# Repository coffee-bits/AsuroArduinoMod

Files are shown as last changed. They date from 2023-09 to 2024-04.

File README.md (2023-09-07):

- [AsuroArduinoMod](#asuroarduinomod)
  - [Goal of the project](#goal-of-the-project)
  - [Problems so far](#problems-so-far)
    - [The old motors are dead](#the-old-motors-are-dead)
  - [State of the project](#state-of-the-project)
    - [Software](#software)
    - [Hardware](#hardware)

# AsuroArduinoMod
> This project is using an Arduino pro micro instead of the original Atmega8L

I own a very old robot education platform called [ASURO](https://de.wikipedia.org/wiki/ASURO)

The main problem using this good old little thing was the old Atmega8L microcontroller platfofm that is programed by avrgcc or Atmel Studio (tm) and loaded by a serial bootloader via an IR light communication channel.

I wanted to bring this in the next level of microcontroller platforms since the modern versions are much easier to use and program. Most of the new platforms unfortunately are using 3.3V but the Asuro has been designed for a logic level of 5V.

My choice was then a Arduino pro micro which uses 5V logic level, has an USB serial interface for communication and program download and its pinning and functionality is quite similar to the Atmega8L.

## Goal of the project
- Replace the old Atmega8L with a "modern" but similar platform: Arduino pro micro instead of the Atmega8L
- create a base system using all the hardware functionalities provided by the Asuro platform
- create a communication interface on the serial port with a simple API procotol to enable other controllers with, for example a WIFI interface or camera, to control the robot platform

## Problems so far
### The old motors are dead
I had to replace the old motors with newer ones. I found a nice and cheap all in one solution...that does not fit and needs a holding frame. So I constructed a frame prototype:

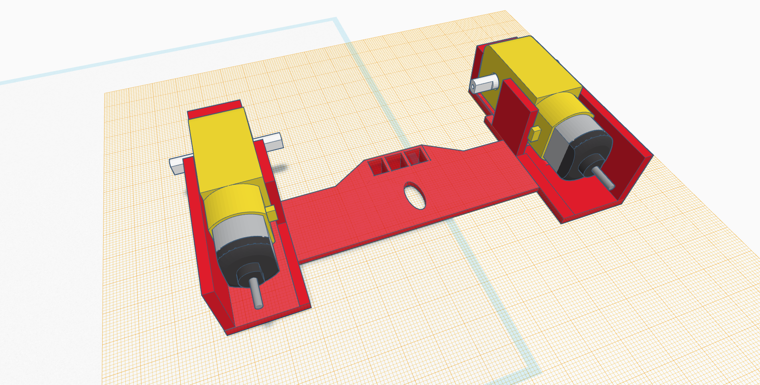
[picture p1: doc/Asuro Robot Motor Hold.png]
Asuro Robot Motor Hold


## State of the project
### Software
The software is currently in experimentl state. All Asuro interfaces are going to be testet with the new connections on the Arduino pro micro. The interface driver functions are going to be rewritten without the usage of the original api.

### Hardware
> connections
All hardware interfaces of the Asuro have been connected to according pins of the Arduino pro micro.

| Pin | Asuro | Arduino | Pin | Asuro | Arduino |
| --- | --- | --- | --- | --- | --- |
| 1 | Rset | \- | 15  | Motor 1 PWM | D6 |
| 2 | IR Receiver<br>SFH5110-36 | D2 | 16  | Motor 2 PWM | D5 |
| 3 | IR Diode -<br>SFH 415-U | GND | 17  | IR Diode +<br>SFH 415-U | D10 |
| 4 | Color LED | D7 | 18  | Motor 2_T7/8 | D13 |
| 5 | Taster Int | D3 | 19  | Motor 2 T5/6 | D9 |
| 6 | Motor 1_T1/2 | D11 | 20  | AVCC | n.a. |
| 7 | VCC | 5V | 21  | Aref | AREF |
| 8 | GND | GND | 22  | AGND | n.a. |
| 9 | Quarz | \- | 23  | Phototransistor T12 analog<br>LPT80A, Fototransistor, farbloses Gehäuse<br>LED D16 +<br>LED 5mm rot | A0 |
| 10  | Quarz | \- | 24  | Phototransistor T11<br>LPT80A, Fototransistor, farbloses Gehäuse<br>LED D15 +<br>LED 5mm rot | A1 |
| 11  | Motor 1_T3/4 | D12 | 25  | Phototransistor T10 analog<br>SFH 300 Fototransistor 5mm | A2 |
| 12  | LED Line | D4 | 26  | Phototransistor T11 analog<br>SFH300, Fototransistor 5mm | A3 |
| 13  | LED 13/14 +<br>IRL80A IR-LED rosafarbenes Gehäuse<br>LED 15/16 -<br>LED 5mm rot | D7 | 27  | Taster Analog Input | A4 |
| 14  | Color LED | D8 | 28  | Spannungsteiler 12k/10k | A5 |

> Prototype state

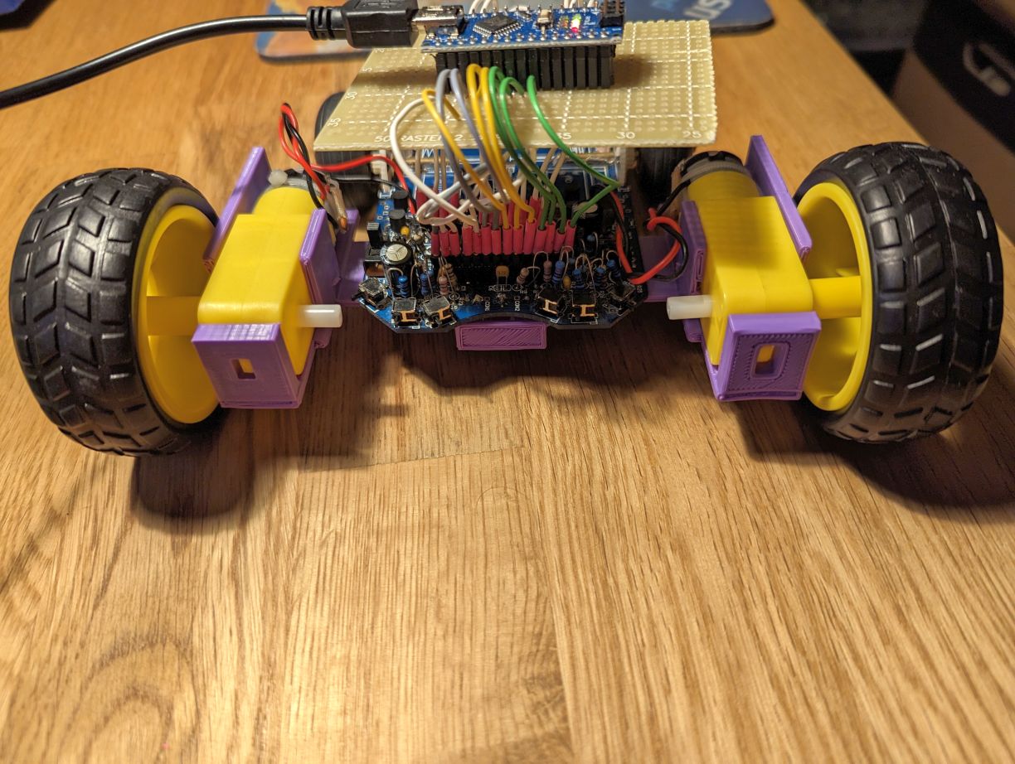
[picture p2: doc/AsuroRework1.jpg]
Asuro Prototype 1.1

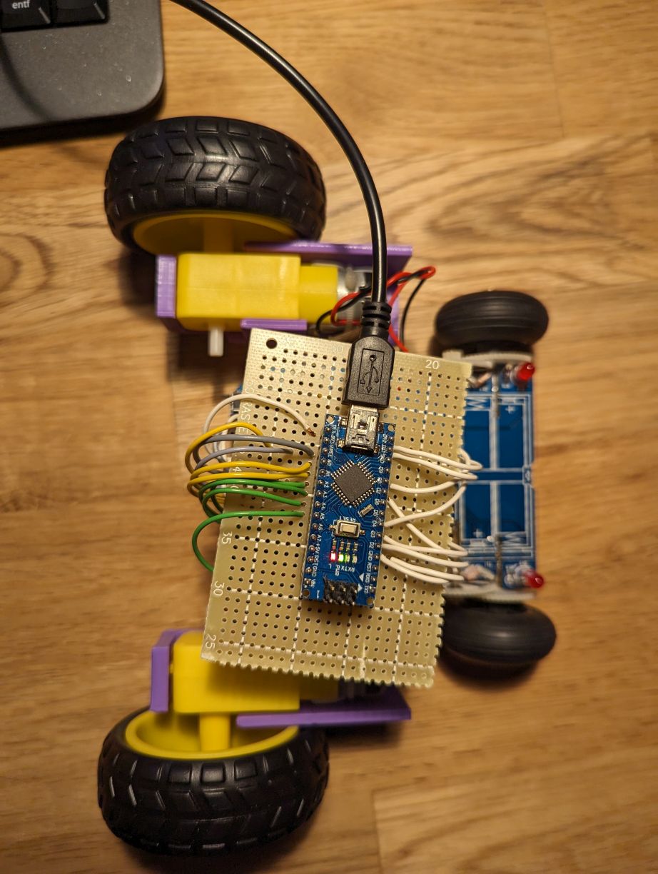
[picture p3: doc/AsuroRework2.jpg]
Asuro Prototype 1.2

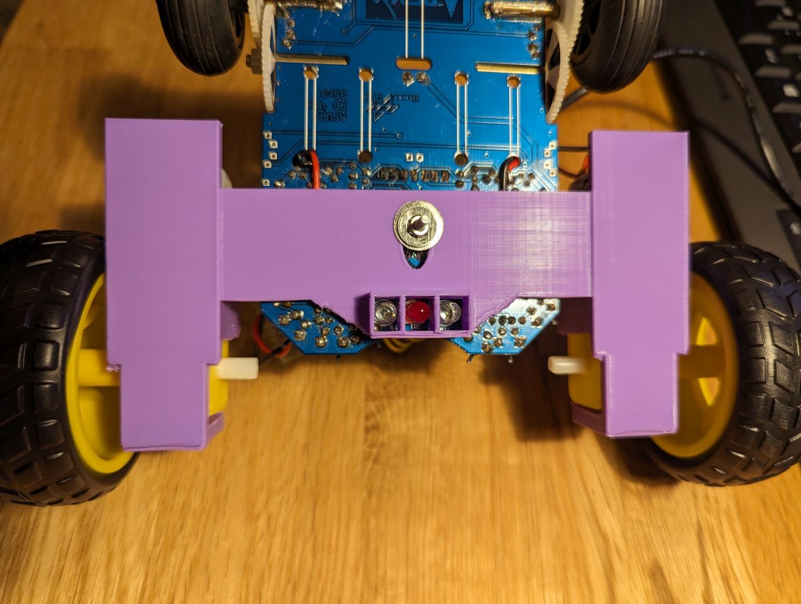
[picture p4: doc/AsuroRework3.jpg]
Asuro Prototype 1.3


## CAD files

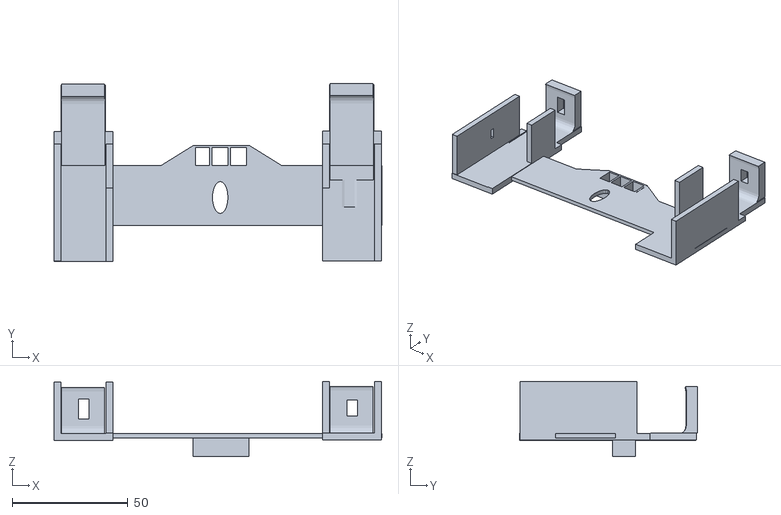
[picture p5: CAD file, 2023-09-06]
hw/Asuro Motor Hold.stl
141.8 x 77.0 x 32.5

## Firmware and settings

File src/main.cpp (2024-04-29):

#include <Arduino.h>

/****************************************************************************
 *   This code is distributed in the hope that it will be useful,           *
 *   but WITHOUT ANY WARRANTY; without even the implied warranty of         *
 *   MERCHANTABILITY or FITNESS FOR A PARTICULAR PURPOSE.                   *
 ****************************************************************************/

/**
 * @file Asuro.ino
 * @author CJ
 * @date March 2023
 * @brief This sketch will use the Arexx Asuro robot platform. 
 * Instead of the original Atmega8L we make use of an Arduino Nano like board  
 * Inspiration https://github.com/Dirk-/Asurino-Library/blob/master/src/Asuro.cpp
 */


constexpr int ASURO_IR_REC_SFH5110_PIN = 2; // Asuro pin 2
// "IR Diode - SFH 415-U" GND                  // Asuro pin 3
constexpr int ASURO_COLOR_LED_RED_PIN = 7; // Asuro pin 4
constexpr int ASURO_SWITCH_INT_PIN = 3; // Asuro pin 5
constexpr int ASURO_MOTOR1_T12_PIN = 11; // Asuro pin 6
// VCC    // Asuro pin 7
// GND    // Asuro pin 8
// quarz  // Asuro pin 9
// quarz  // Asuro pin 10
constexpr int ASURO_MOTOR1_T34_PIN = 12; // Asuro pin 11
constexpr int ASURO_LINE_LED_PIN = 4; // Asuro pin 12
constexpr int ASURO_LED13_14_POS_PIN = A7; //? Asuro pin 13
constexpr int ASURO_LED15_16_NEG_PIN = A7; //? Asuro pin 13
constexpr int ASURO_COLOR_LED_GREEN_PIN = 8; // Asuro pin 14
// #####
constexpr int ASURO_MOTOR1_PWM_PIN = 6; // Asuro pin 15
constexpr int ASURO_MOTOR2_PWM_PIN = 5; // Asuro pin 16
constexpr int ASURO_IR_TRANSMITTER_PIN = 10; // Asuro pin 17
constexpr int ASURO_MOTOR2_T78_PIN = 13; // Asuro pin 18
constexpr int ASURO_MOTOR2_T56_PIN = 9; // Asuro pin 19
// AVCC    // Asuro pin 20
// AREF    // Asuro pin 21
// AGND    // Asuro pin 22
constexpr int ASURO_PHOTO_T12_PIN = A0; // Asuro pin 23
constexpr int ASURO_LED16_POS_PIN = A0; // Asuro pin 23
constexpr int ASURO_PHOTO_T11_PIN = A1; // Asuro pin 24
constexpr int ASURO_LED15_POS_PIN = A1; // Asuro pin 24
constexpr int ASURO_PHOTO_T10_PIN = A2; // Asuro pin 25
constexpr int ASURO_PHOTO_T9_PIN = A3; // Asuro pin 26
constexpr int ASURO_SWITCHES_PIN = A4; // Asuro pin 27
constexpr int ASURO_DIVIDER_PIN = A5; // Asuro pin 28

/**
 * @brief color LED color
 * 
 */
enum class LED_COLOR_EN{
  LED_COLOR_RED = 0,
  LED_COLOR_GREEN = 1,
  LED_COLOR_YELLOW = 2
};

/**
 * @brief digital state, for example LED on or off
 * 
 */
enum class IO_STATE_EN{
  IO_STATE_ON = 0,
  IO_STATE_OFF = 1,
  IO_STATE_UNDEF = 2
};

/**
 * @brief line sensor selection
 * 
 */
enum class LINE_SENSOR_EN{
  LINE_SENSOR_LEFT = 0,
  LINE_SENSOR_RIGHT = 1,
  LINE_SENSOR_BOTH = 2,
  LINE_SENSOR_UNDEF = 3,
};

/**
 * @brief motor parameters
 * 
 */
struct MOTOR_SELECTION_ST{
  int16_t left_motor_speed;
  int16_t right_motor_speed;
};


void Asuro_setMotor(struct MOTOR_SELECTION_ST paramMotorSelection);
void Asuro_initBackLeds(void);
void Asuro_setBackLeds(enum IO_STATE_EN paramLeftLedState, enum IO_STATE_EN paramRightLedState);



/**
 * @brief main Arduino setup routine
 * It initializes and test the main Asuro funktions
 * 
 */
void setup() {
  int tempReadTestValue = 0;
  // init serial interface  
  Serial.begin(9600);

  // initial self test of color LED
  // ##############################
   Serial.println("Set Color LED red to output");
   pinMode(ASURO_COLOR_LED_RED_PIN, OUTPUT);
   Serial.println("Set Color LED red to high");
   digitalWrite(ASURO_COLOR_LED_RED_PIN, HIGH);
   delay(1000);                       // wait for a second
   Serial.println("Set Color LED red to low");
   digitalWrite(ASURO_COLOR_LED_RED_PIN, LOW);
   delay(1000);                       // wait for a second
   Serial.println("Set Color LED green to output");
   pinMode(ASURO_COLOR_LED_GREEN_PIN, OUTPUT);
   Serial.println("Set Color LED green to high");
   digitalWrite(ASURO_COLOR_LED_GREEN_PIN, HIGH);
   delay(1000);                       // wait for a second
   Serial.println("Set Color LED green to low");
   digitalWrite(ASURO_COLOR_LED_GREEN_PIN, LOW);
   delay(1000);                       // wait for a second
  // initial self test of line LED and line photo read
  // #################################################
   Serial.println("Set line LED to output");
   pinMode(ASURO_LINE_LED_PIN, OUTPUT);
   Serial.println("Set line LED to high");
   digitalWrite(ASURO_LINE_LED_PIN, HIGH);
   Serial.print("Read Line 1: ");
   tempReadTestValue = analogRead(ASURO_PHOTO_T10_PIN);
   Serial.println(tempReadTestValue);
   Serial.print("Read Line 2: ");
   tempReadTestValue = analogRead(ASURO_PHOTO_T9_PIN);
   Serial.println(tempReadTestValue);
   delay(1000);                       // wait for a second
   digitalWrite(ASURO_LINE_LED_PIN, LOW);
   Serial.print("Read Line 1: ");
   tempReadTestValue = analogRead(ASURO_PHOTO_T10_PIN);
   Serial.println(tempReadTestValue);
   Serial.print("Read Line 2: ");
   tempReadTestValue = analogRead(ASURO_PHOTO_T9_PIN);
   Serial.println(tempReadTestValue);
   delay(1000);

  // initialize back LEDs
  Asuro_initBackLeds();
  delay(5000);
  Asuro_setBackLeds(IO_STATE_EN::IO_STATE_ON, IO_STATE_EN::IO_STATE_OFF);
  delay(5000);
  Asuro_setBackLeds(IO_STATE_EN::IO_STATE_OFF, IO_STATE_EN::IO_STATE_ON);
  delay(5000);
  Asuro_setBackLeds(IO_STATE_EN::IO_STATE_ON, IO_STATE_EN::IO_STATE_ON);
  delay(5000);
  Asuro_setBackLeds(IO_STATE_EN::IO_STATE_OFF, IO_STATE_EN::IO_STATE_OFF);

  // initialize motore functions
  struct MOTOR_SELECTION_ST tempMotorSelection;
  tempMotorSelection.left_motor_speed = 180;
  tempMotorSelection.right_motor_speed = -180;
  Asuro_setMotor(tempMotorSelection);
  delay(10000);
  tempMotorSelection.left_motor_speed = 0;
  tempMotorSelection.right_motor_speed = 0;
  Asuro_setMotor(tempMotorSelection);
  delay(10000);
  tempMotorSelection.left_motor_speed = -180;
  tempMotorSelection.right_motor_speed = 180;
  Asuro_setMotor(tempMotorSelection);
  delay(10000);
  tempMotorSelection.left_motor_speed = 0;
  tempMotorSelection.right_motor_speed = 0;
  Asuro_setMotor(tempMotorSelection);
  
}

/**
 * @brief main Arduino loop
 * it schedules the Asuro tasks
 * 
 */
void loop() {
  // put your main code here, to run repeatedly:

}


void Asuro_initBackLeds(void)
{
  Serial.println("Set direction for LED15/16 neg. side to output");
  pinMode(ASURO_LED15_16_NEG_PIN, OUTPUT);
  Serial.println("Set level for LED15/16 neg. side to low");
  digitalWrite(ASURO_LED15_16_NEG_PIN, LOW);

  Serial.println("Set LED15 pin direction to output");
  pinMode(ASURO_LED15_POS_PIN, OUTPUT);
  Serial.println("Set LED15 pin low level");
  digitalWrite(ASURO_LED15_POS_PIN, LOW);

  Serial.println("Set LED15 pin direction to output");
  pinMode(ASURO_LED16_POS_PIN, OUTPUT);
  Serial.println("Set LED16 pin low level");
  digitalWrite(ASURO_LED16_POS_PIN, LOW);
}


/**
 * @brief Function to set the back LEDs to a given level (high or low)
 * 
 * @param paramLeftLedState set left LED to IO_STATE_EN::IO_STATE_ON or _OFF 
 * @param paramRightLedState set right LED to IO_STATE_EN::IO_STATE_ON or _OFF
 */
void Asuro_setBackLeds(enum IO_STATE_EN paramLeftLedState, enum IO_STATE_EN paramRightLedState)
{
  Serial.println("Set direction for LED15/16 neg. side to output");
  pinMode(ASURO_LED15_16_NEG_PIN, OUTPUT);
  Serial.println("Set level for LED15/16 neg. side to low");
  digitalWrite(ASURO_LED15_16_NEG_PIN, LOW);

  Serial.println("Set LED15 pin direction to output");
  pinMode(ASURO_LED15_POS_PIN, OUTPUT);
  if (IO_STATE_EN::IO_STATE_ON == paramLeftLedState){
    Serial.println("Set LED15 pin high level");
    digitalWrite(ASURO_LED15_POS_PIN, HIGH);
  
  } else {
    Serial.println("Set LED15 pin low level");
    digitalWrite(ASURO_LED15_POS_PIN, LOW);
  }
  if (IO_STATE_EN::IO_STATE_ON == paramRightLedState){
    Serial.println("Set LED16 pin high level");
    digitalWrite(ASURO_LED16_POS_PIN, HIGH);
  
  } else {
    Serial.println("Set LED16 pin low level");
    digitalWrite(ASURO_LED16_POS_PIN, LOW);
  }
}

/**
 * @brief inits the color LED with red and green and sets the output to low
 * 
 */
void Asuro_initColorLed(void){
  Serial.println("Set Color LED red to output");
  pinMode(ASURO_COLOR_LED_RED_PIN, OUTPUT);
  Serial.println("Set Color LED red to low");
  digitalWrite(ASURO_COLOR_LED_RED_PIN, LOW);
  Serial.println("Set Color LED green to output");
  pinMode(ASURO_COLOR_LED_GREEN_PIN, OUTPUT);
  Serial.println("Set Color LED green to low");
  digitalWrite(ASURO_COLOR_LED_GREEN_PIN, LOW);
}

/**
 * @brief set the color and state (on/off) of the color LED
 * 
 * @param paramLedColor LED_COLOR_RED, LED_COLOR_GREEN, LED_COLOR_YELLOW 
 * @param paramIoState IO_STATE_ON, IO_STATE_OFF
 */
void Asuro_setColorLed(enum LED_COLOR_EN paramLedColor, enum IO_STATE_EN paramIoState){

  switch (paramLedColor){
    case LED_COLOR_EN::LED_COLOR_RED:
    if (IO_STATE_EN::IO_STATE_ON == paramIoState){
      digitalWrite(ASURO_COLOR_LED_RED_PIN, HIGH);
    }
    else{
      digitalWrite(ASURO_COLOR_LED_RED_PIN, LOW);
    }
    break;
  case LED_COLOR_EN::LED_COLOR_GREEN:
    if (IO_STATE_EN::IO_STATE_ON == paramIoState){
      digitalWrite(ASURO_COLOR_LED_GREEN_PIN, HIGH);
    }
    else{
      digitalWrite(ASURO_COLOR_LED_GREEN_PIN, LOW);
    }
    break;
  case LED_COLOR_EN::LED_COLOR_YELLOW:
    if (IO_STATE_EN::IO_STATE_ON == paramIoState){
      digitalWrite(ASURO_COLOR_LED_RED_PIN, HIGH);
      digitalWrite(ASURO_COLOR_LED_GREEN_PIN, HIGH);
    }
    else{
      digitalWrite(ASURO_COLOR_LED_RED_PIN, LOW);
      digitalWrite(ASURO_COLOR_LED_GREEN_PIN, LOW);  
    }
    break;
  default:
    break;
  }
}

/**
 * @brief set line LED
 * 
 * @param paramIoState IO_STATE_ON, IO_STATE_OFF
 */
void Asuro_setLineLed(enum IO_STATE_EN paramIoState){

  if (IO_STATE_EN::IO_STATE_ON == paramIoState){
    digitalWrite(ASURO_LINE_LED_PIN, HIGH);
  }
  else{
    digitalWrite(ASURO_LINE_LED_PIN, LOW);
  }
}



/**
 * @brief reads the line sensor data
 * 
 * @param paramLineSensor LINE_SENSOR_LEFT, LINE_SENSOR_RIGHT, LINE_SENSOR_BOTH
 * @return -1 in case of a parameter error, else sensor data
 */
int Asuro_readLineSensor(enum LINE_SENSOR_EN paramLineSensor){
  int tempReadSensorValue = 0;
  switch (paramLineSensor){
    case LINE_SENSOR_EN::LINE_SENSOR_LEFT:
      tempReadSensorValue = analogRead(ASURO_PHOTO_T10_PIN);
    break;

    case LINE_SENSOR_EN::LINE_SENSOR_RIGHT:
      tempReadSensorValue = analogRead(ASURO_PHOTO_T9_PIN);
    break;

    case LINE_SENSOR_EN::LINE_SENSOR_BOTH:
      tempReadSensorValue = analogRead(ASURO_PHOTO_T9_PIN);
      tempReadSensorValue += analogRead(ASURO_PHOTO_T10_PIN);
      tempReadSensorValue = tempReadSensorValue / 2;
    break;

    default:
      tempReadSensorValue = -1;
    break;  
  }
   
   
  return tempReadSensorValue;
}


/**
 * @brief set Motor Parameters
 * 
 * @param paramMotorSelection left motor speed and right motor speed, values higher than 255 are truncated, positive values direct foward, nagative backward and 0 stops
 * 
 * http://www.asurowiki.de/pmwiki/pmwiki.php/Main/Motorbruecke
 * Funktion	PD5 (PB5)	PD4 (PB4)
 * vorwärts	  1	        0
 * rückwärts  0	        1
 * bremsen	  0	        0
 * leerlauf	  1	        1
 * 
 */
void Asuro_setMotor(struct MOTOR_SELECTION_ST paramMotorSelection){
  Serial.print("Input-Parameter: ");
  Serial.print(paramMotorSelection.left_motor_speed);
  Serial.print(",");
  Serial.println(paramMotorSelection.right_motor_speed);
  
  uint16_t tempMotorSpeedLeftConversion = abs(paramMotorSelection.left_motor_speed) & 0xFF;
  uint16_t tempMotorSpeedRightConversion = abs(paramMotorSelection.right_motor_speed) & 0xFF;

  Serial.println("Set Motor Parameters");
  pinMode(ASURO_MOTOR1_T12_PIN, OUTPUT);
  pinMode(ASURO_MOTOR1_T34_PIN, OUTPUT);
  pinMode(ASURO_MOTOR1_PWM_PIN, OUTPUT);
  pinMode(ASURO_MOTOR2_T78_PIN, OUTPUT);
  pinMode(ASURO_MOTOR2_T56_PIN, OUTPUT);  
  pinMode(ASURO_MOTOR2_PWM_PIN, OUTPUT);

  if (paramMotorSelection.left_motor_speed > 0){
    Serial.print("left motor speed > 0: T12=high;T34=low: ");
    Serial.println(tempMotorSpeedLeftConversion);
    digitalWrite(ASURO_MOTOR1_T12_PIN, HIGH);
    digitalWrite(ASURO_MOTOR1_T34_PIN, LOW);
    analogWrite(ASURO_MOTOR1_PWM_PIN,tempMotorSpeedLeftConversion);
  }
  else if (paramMotorSelection.left_motor_speed < 0){
    Serial.print("left motor speed < 0: T12=low;T34=high: -");
    Serial.println(tempMotorSpeedLeftConversion);
    digitalWrite(ASURO_MOTOR1_T12_PIN, LOW);
    digitalWrite(ASURO_MOTOR1_T34_PIN, HIGH);
    analogWrite(ASURO_MOTOR1_PWM_PIN,tempMotorSpeedLeftConversion);
  } else {
    Serial.println("left motor speed < 0: T12=low;T34=low: 0");
    digitalWrite(ASURO_MOTOR1_T12_PIN, LOW);
    digitalWrite(ASURO_MOTOR1_T34_PIN, LOW);
    analogWrite(ASURO_MOTOR1_PWM_PIN,0);
  }

  if (paramMotorSelection.right_motor_speed > 0){
    Serial.print("right motor speed > 0: T78=high;T56=low: ");
    Serial.println(tempMotorSpeedRightConversion);
    digitalWrite(ASURO_MOTOR2_T78_PIN, HIGH);
    digitalWrite(ASURO_MOTOR2_T56_PIN, LOW);
    analogWrite(ASURO_MOTOR2_PWM_PIN,tempMotorSpeedRightConversion);
  }
  else if (paramMotorSelection.right_motor_speed < 0){
    Serial.print("right motor speed < 0: T78=low;T56=high: -");
    Serial.println(tempMotorSpeedRightConversion);
    digitalWrite(ASURO_MOTOR2_T78_PIN, LOW);
    digitalWrite(ASURO_MOTOR2_T56_PIN, HIGH);
    analogWrite(ASURO_MOTOR2_PWM_PIN,tempMotorSpeedRightConversion);
  } else {
    Serial.println("right motor speed < 0: T78=low;T56=low: 0");
    digitalWrite(ASURO_MOTOR2_T78_PIN, LOW);
    digitalWrite(ASURO_MOTOR2_T56_PIN, LOW);
    analogWrite(ASURO_MOTOR2_PWM_PIN,0);
  }

}

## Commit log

2023-04-18 additional functions setting color LED, line LED and read line sensor
2023-05-23 Preparation for Motor operation
2023-05-29 Motor control function defined
2023-06-17 added Functions to set Motor und Back LEDs and included them to the initialization routine
2023-09-06 3d printable motor hold frame for replacement motor
    [Asuro Motor Hold.stl]
2023-09-06 more details in the README.md -project description - motor frame
2023-09-07 additional project information on HW pinning and prototype state
2023-11-01 fixed Motor behavior. Motors spinning correctly in both directions and stop.
    [main.cpp]
2024-04-29 Back LEDs working and test sequence in initialisation function
